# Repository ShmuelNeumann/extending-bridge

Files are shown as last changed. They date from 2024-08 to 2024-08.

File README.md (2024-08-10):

# Extending Bridge
## Overview
**Starting Date:** July 2022

**Project Completion:** October 2022

**Motivation:** University Assignment

**Status:** Complete

This was a project I worked on in my first year of university to design and build an extending bridge. Although I've completed a lot of projects during my degree, this is one I'm very proud of.

It was created in collaboration with the students Rex Buckle, Dev Kalsi, Tinotenda Mapani and Sofia Lopez.

## Context

This project was completed as part of my first year ENG1011 Engineering Methods unit.

We were tasked with designing an extending bridge that fit within a 100x100x100mm cube when retraced and could span a 300mm gap when fully extended. The bridge also had to be able to support a 1kg load, and be opened with a hex key.

The design was modeling in SolidWorks, printed in PLA, and then assembled with screws, axles, and nuts.

I had a lot of experience with 3d modeling in Blender3d as a hobby before starting this project, so I used this expertise to complete the majority of the SolidWorks modeling for this project.
In particular, I found the spatial reasoning skills I had gained and the speed I was able to use the program was a large benefit to the team.

## Design and Features

The bridge was composed of two frames on each end, with a scissor mechanism between them.
When closed these two frames form a cube, with the scissor mechanism enclosed within them.

The SolidWorks model fully extended

The SolidWorks model fully retracted

One of the frames is the smaller follower frame, which ensures that side of the bridge can actuate freely while keeping the frame perpendicular to the scissor mechanism.
This is achieved by having the upper joints of the scissor constrained to only rotating, while the lower joints are allowed to move vertically on a track. This track also stops the scissor from overextending.

Diagram of the follower frame

The other is the larger driver frame, and it contains the mechanism to extend the scissor.
Once again the top joints are pinned in place, however for this frame the lower joints are connected to a rack and pinion mechanism.
The scissor joint connects to a set of racks that travels vertically along a track when the pinion gear shaft is rotated with a hex key.

Model of the driver frame, with it's rack and pinion mechanism

Model of the gear shaft and racks that make up the mechanism

One feature of the design I was very happy with was the gear shaft.
This was composed of 3 separate pieces that were held  together by the side frames.
This made the printing easier as we could print each part in whatever orientation worked best for it, instead of all facing the same way.
This also allowed us to quickly replace subparts of it when they broke during testing, without needing to reprint the entire part.



## Results

After a few minor issues, this design worked excellently. The opening mechanism worked as expected and it easily managed the load requirement.
This design stood out from the other student's for a few reasons. One was that ours was capable of both extending and retracting, unlike a number of other designs that utilised elastic bands or other mechanisms that could only be deployed once and not retracted. Another was that our bridge had the frame integrated into it whereas most others just had an exposed mechanism.

Overall I was very proud of this design and happy with how it turned out.



A video of the opening sequence can be found below.

## Issues and Future Improvements
### 3d Printing Efficiency
One lesson I learnt very early on was to keep the printing time as low as possible. This design took 8.5 hours to print, and this was after I reduced the design to remove unnecessary solid segments.

This image shows an early model before we removed the unnecessary parts.



I also learnt the importance of understanding the printer options and setting them right the first time instead of wasting time with failed prints. When printing out the gear, which was the most complex part, we struggled to get the hex socket to be the right size. After several redesigns and a lot of time, we finally realised that the design was fine. It was the printer's filament width setting being too high, which meant the accuracy wasn't enough. Once this was fixed the design worked perfectly.



### Fail Fast

An unforeseen issue we encountered was that we were unable to test if this design would work and be able to carry the load until after it was printed.
This meant if it did fail, we wouldn't be able to redesign and print a new version before the deadline.

In the end this design did succeed admirably. However it came close to failing when the rack would loose traction with the pinion gear due to the PLA bending under the load. This was fixed by printing and adding a bracket that stopped the rack from bending, however this could have required a major redesign.

It was a important reminder of the engineering principle of "Fail Fast", or testing in increments so if the design failed it would fail quickly before we invested too much time into it.
In the future I would just design a mounting for the mechanism without printing the rest of the frames to ensure it worked. I would only commit to printing the larger frames once I was sure the mechanism worked and was sttrong enough.

## Viewing the Model
The SolidWork model are available in this repository, and have been tested in SolidWorks 2024.

The main assembly file is:
ScissorBridgeFinal.SLDASM

## Further Links
- [Video of Bridge Deployment](https://1drv.ms/v/s!AsGj4vURYEC-sepVkZ4p2qBsM1MrJg?e=dqk6c2)
- [Slides used during pitch presentation.](https://1drv.ms/p/s!AsGj4vURYEC-sepWxoLERqLRnZ4RdQ?e=KtqlJ5) (Note that team member pictures have been removed for privacy)

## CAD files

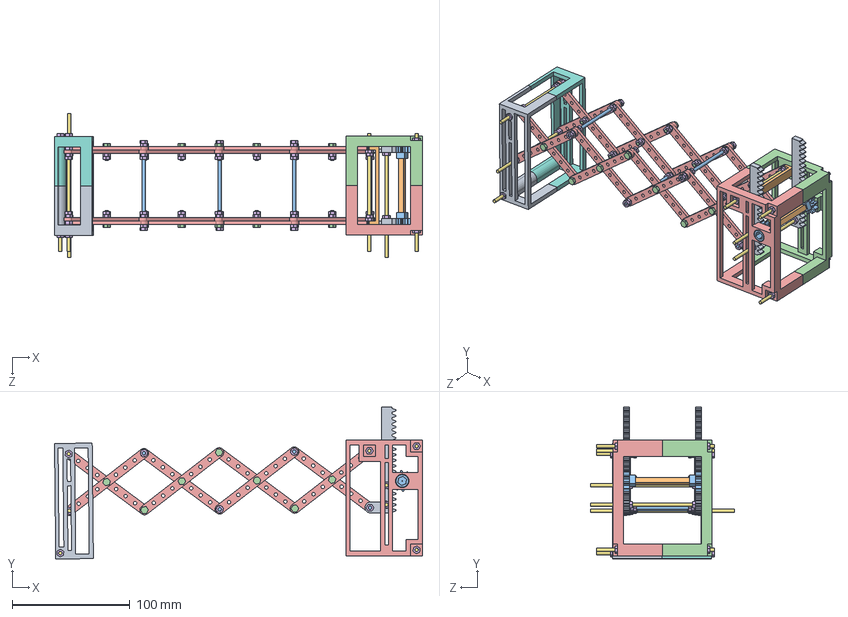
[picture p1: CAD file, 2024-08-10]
ExtendingBridgeModel/ScissorBridgeFinal.SLDASM
312.1 x 128.9 x 122.0 mm
InvertedLargeFrameRight
LargeFrameRight
Gear x 2
squareRod
InvertedLargeFrameLeft
LargeFrameLeft
100mmRod x 9
M3_nut x 104
9 Hole x 16
M3_12mm_bolt x 14
75mmRod x 5
ShmuelNeumann_33109168_angleBracket
InvertedRack x 2

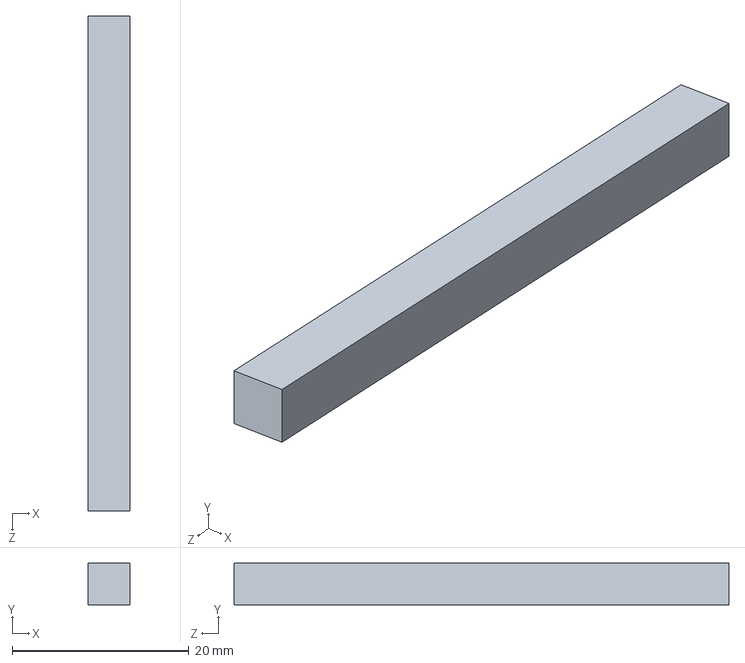
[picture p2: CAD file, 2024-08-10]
ExtendingBridgeModel/squareRod.SLDPRT
4.70 x 4.70 x 56.0 mm

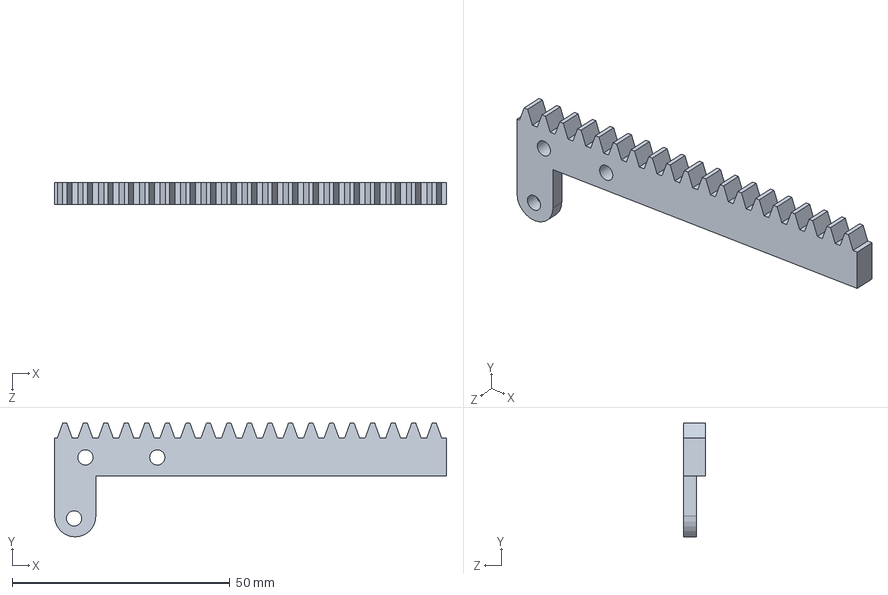
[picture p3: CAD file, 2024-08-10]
ExtendingBridgeModel/Rack.SLDPRT
90.0 x 26.1 x 5.00 mm

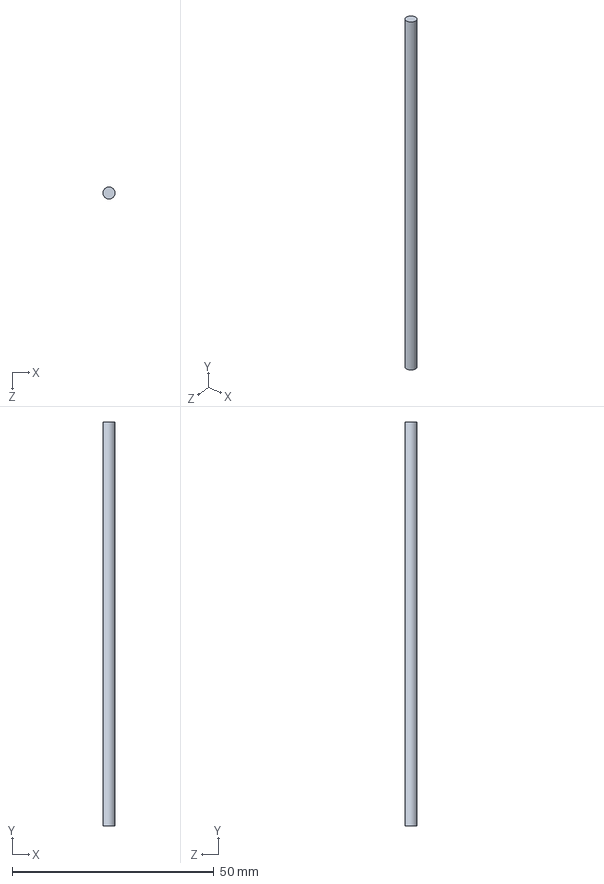
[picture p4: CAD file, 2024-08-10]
ExtendingBridgeModel/100mmRod.SLDPRT
3.00 x 100.0 x 3.00 mm

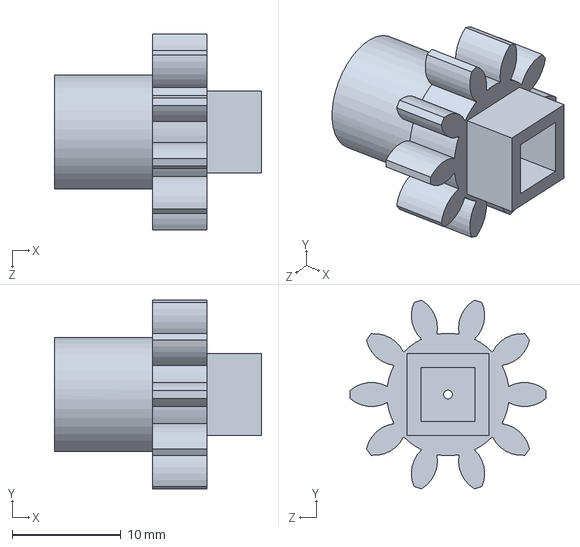
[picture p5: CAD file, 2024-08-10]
ExtendingBridgeModel/Gear.SLDPRT
19.0 x 17.3 x 18.0 mm

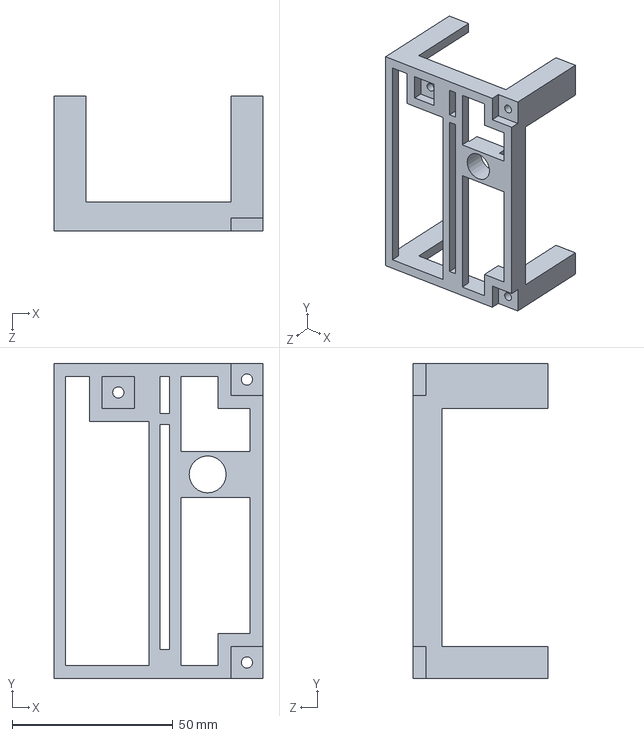
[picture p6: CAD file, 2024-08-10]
ExtendingBridgeModel/InvertedLargeFrameRight.SLDPRT
65.0 x 98.0 x 42.0 mm

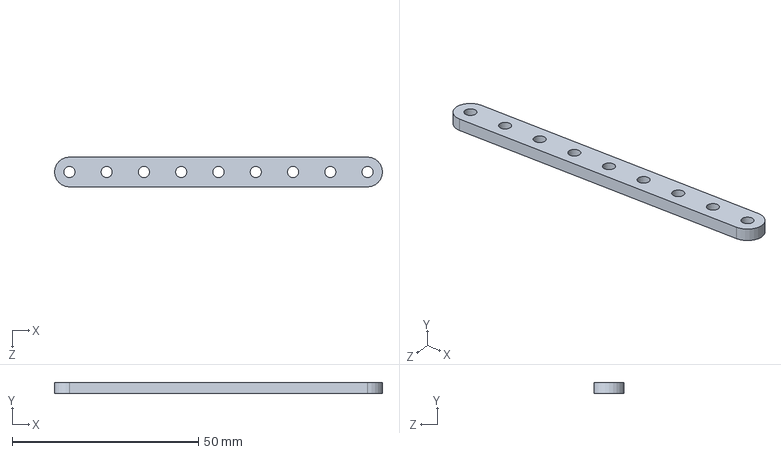
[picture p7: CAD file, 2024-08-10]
ExtendingBridgeModel/9 Hole.SLDPRT
88.0 x 3.00 x 8.00 mm

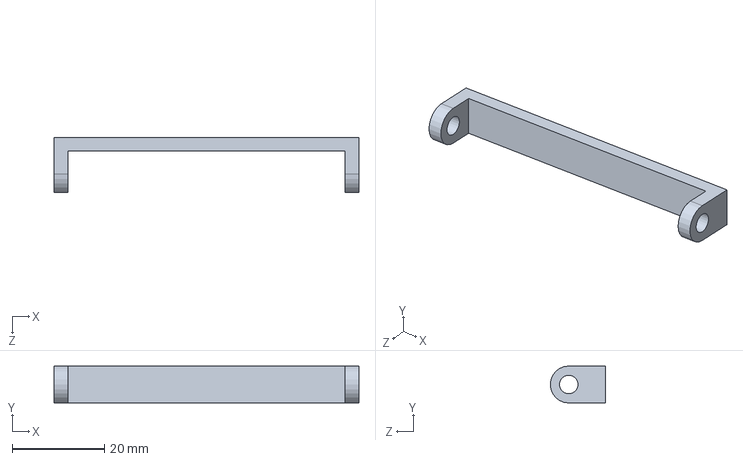
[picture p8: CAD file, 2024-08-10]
ExtendingBridgeModel/ShmuelNeumann_33109168_angleBracket.SLDPRT
66.0 x 8.00 x 12.0 mm

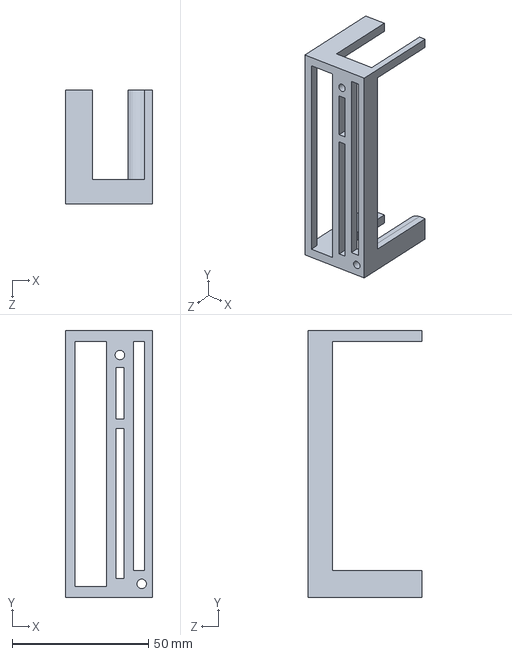
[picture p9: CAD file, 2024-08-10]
ExtendingBridgeModel/LargeFrameLeft.SLDPRT
32.0 x 98.0 x 42.0 mm

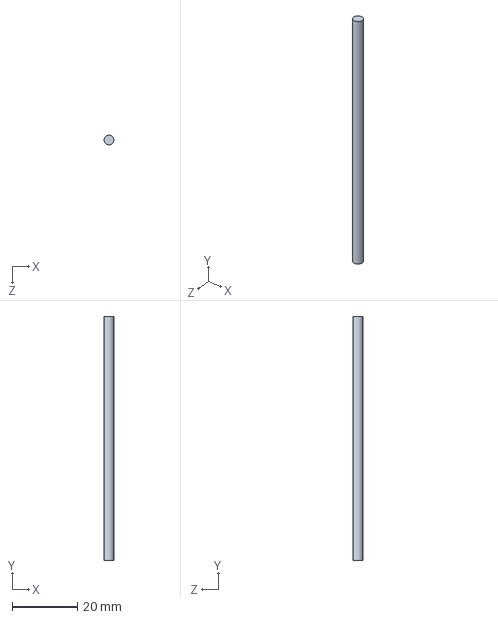
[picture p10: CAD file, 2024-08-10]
ExtendingBridgeModel/75mmRod.SLDPRT
3.00 x 75.0 x 3.00 mm

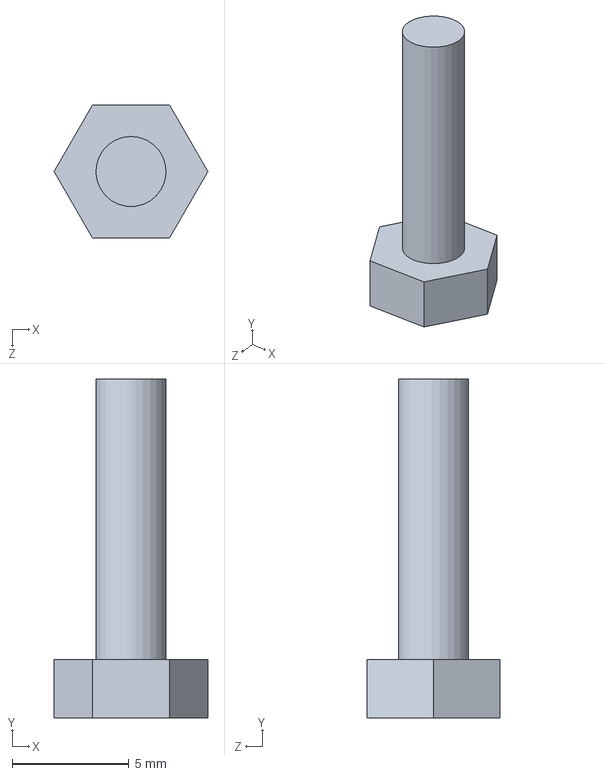
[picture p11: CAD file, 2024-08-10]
ExtendingBridgeModel/M3_12mm_bolt.SLDPRT
6.58 x 14.5 x 5.70 mm

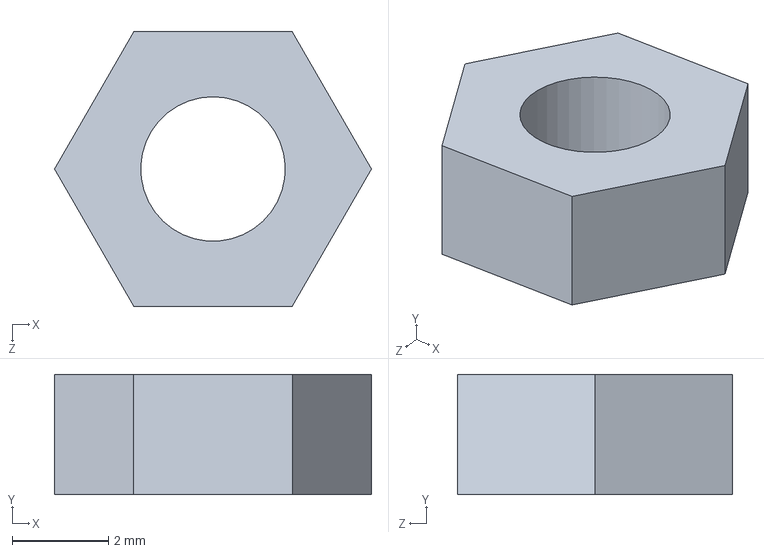
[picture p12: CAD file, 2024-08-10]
ExtendingBridgeModel/M3_nut.SLDPRT
6.58 x 2.50 x 5.70 mm

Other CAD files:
ExtendingBridgeModel/InvertedRack.SLDPRT
ExtendingBridgeModel/LargeFrameRight.SLDPRT
ExtendingBridgeModel/InvertedLargeFrameLeft.SLDPRT
